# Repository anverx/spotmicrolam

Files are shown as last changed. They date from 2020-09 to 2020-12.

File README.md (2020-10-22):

# spotmicrolam
SportMicroAI the lean and mean edition.
The design is inspired by MicroSpotAI but developed from scratch.
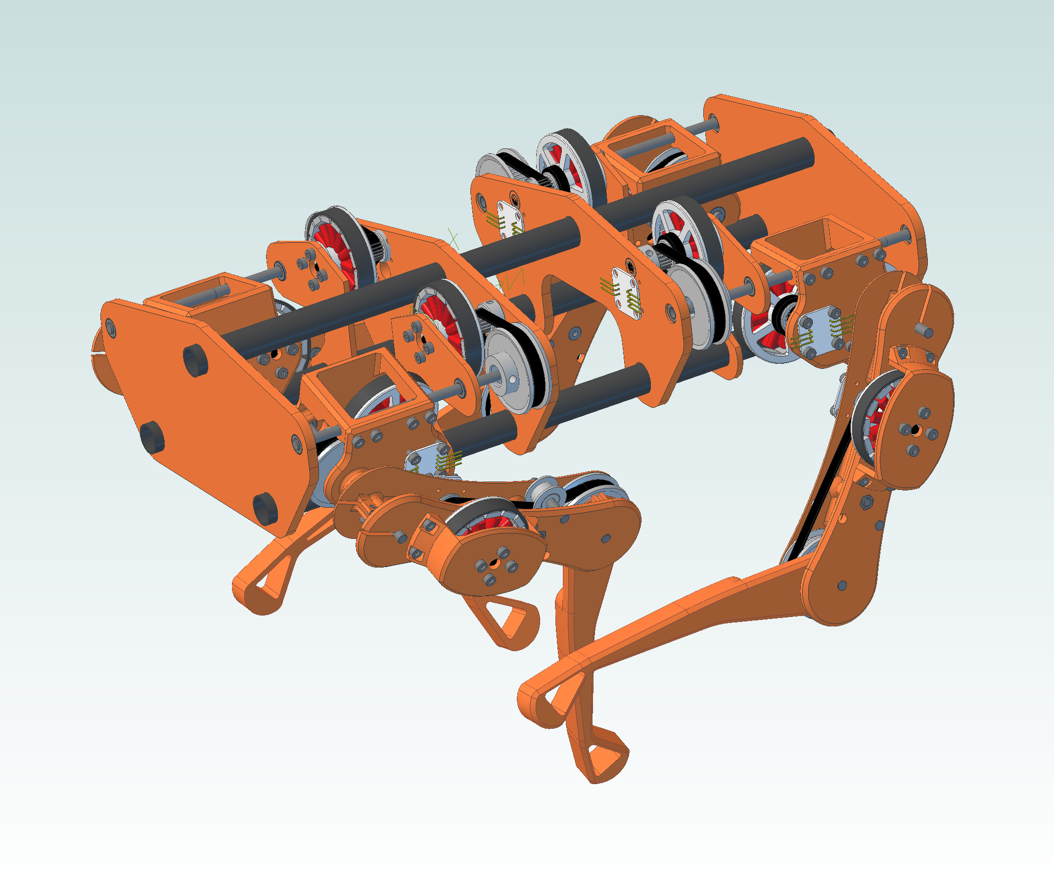
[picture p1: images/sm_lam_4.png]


## Design goals of the project:
* Cheap, under 500e, ideally towards 300e
* Off the shelf components and 3D printed parts only
* Designed parts optimized for easy printing, minimal or no supports
* Optimize for weight as the motors are underpowered
* bldc motors

## Challenges:
At the moment the biggest challenge are the motor drivers.  There are plenty of cheap brushless motors for aircrafts, and they should work fine.  
The ESC however are geared towards flying, they offer no reverse rotation or holding torque.  Finding the right ESCs and controlling them is an interesing excersize. 

## Key Ingredients
* 5010 BLDC motors, ~14e per piece
* Some bldc driver ~10e per piece if i can make HMBGC work, may need something else for more current
* Rotary encoder, at the moment AS5600 (single i2c adderess? meh), readymade module (~2e a piece)
* Bearings, pulleys, belts, shafts etc. under 30e per leg
* Carbon fiber pipes for body structure ~40e
* Raspberry Pi or Orange Pi + arduino clone for the brain ~40e

So, 26e (per motor) x 12 = 312
30e (per leg) x 4 = 120

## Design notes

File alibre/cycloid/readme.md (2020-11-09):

# Poorman's guide to calculating the cycloid disk shapes

[//]: # (This is a comment)

* There are some good references
  * [video on cycloids](https://www.youtube.com/watch?v=SWIx3GgqrAg)
  * [cycloid disk design in fusion](https://www.youtube.com/watch?v=jQ6LQBFZXmU)

* Compute the formulas using [the calculator](http://www.otvinta.com/cycloid.html), you will need the following parameters:
  * outer diameter
  * pin diameter
  * pin number
  * excentricity
* Graph the firmulas and save as svg using an online [graphing calulator](http://fooplot.com/)
  * use the parametric plot option
  * paste the formulas for x and y from the previous steps (change `u` to `s` where appropriate)
  * set s from 0 to 1 (plus 1 step),  set the step to 0.001 (or less)
  * in the display section untick grid, axes, tick marks and numbers

* If your CAD is unhappy with svgs [convert to dxf](https://cloudconvert.com/svg-to-dxf)
> after all Alibre is unable to assimilate splines generated with external applications, bummer

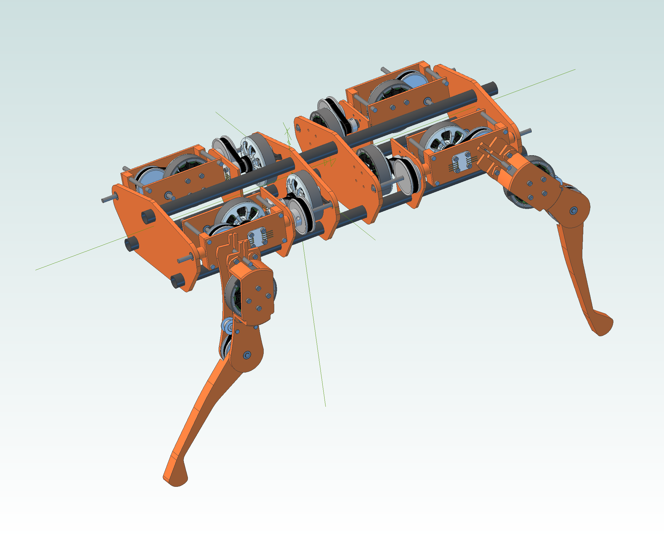
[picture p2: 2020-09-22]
images/sma_lam.png

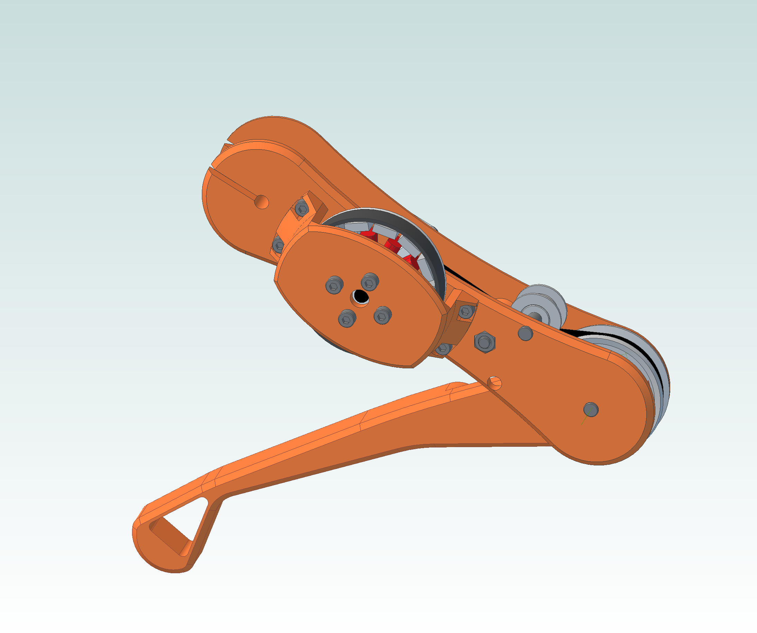
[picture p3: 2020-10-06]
images/Leg.png

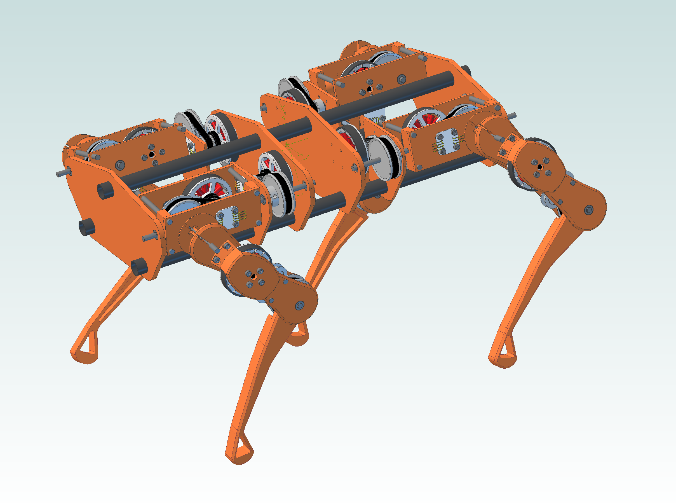
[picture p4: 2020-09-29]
images/sma_lam_2.png

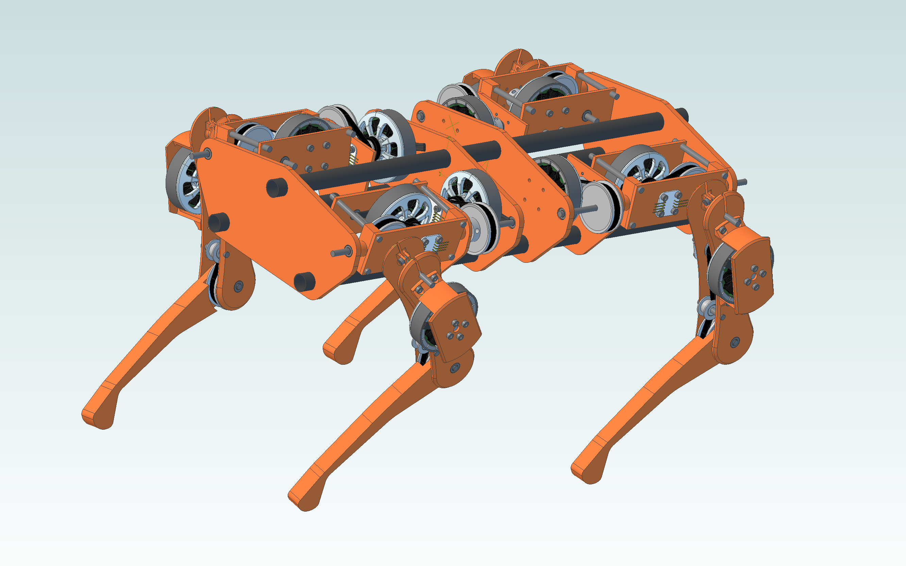
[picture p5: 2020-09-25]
images/sma_lam_1.png

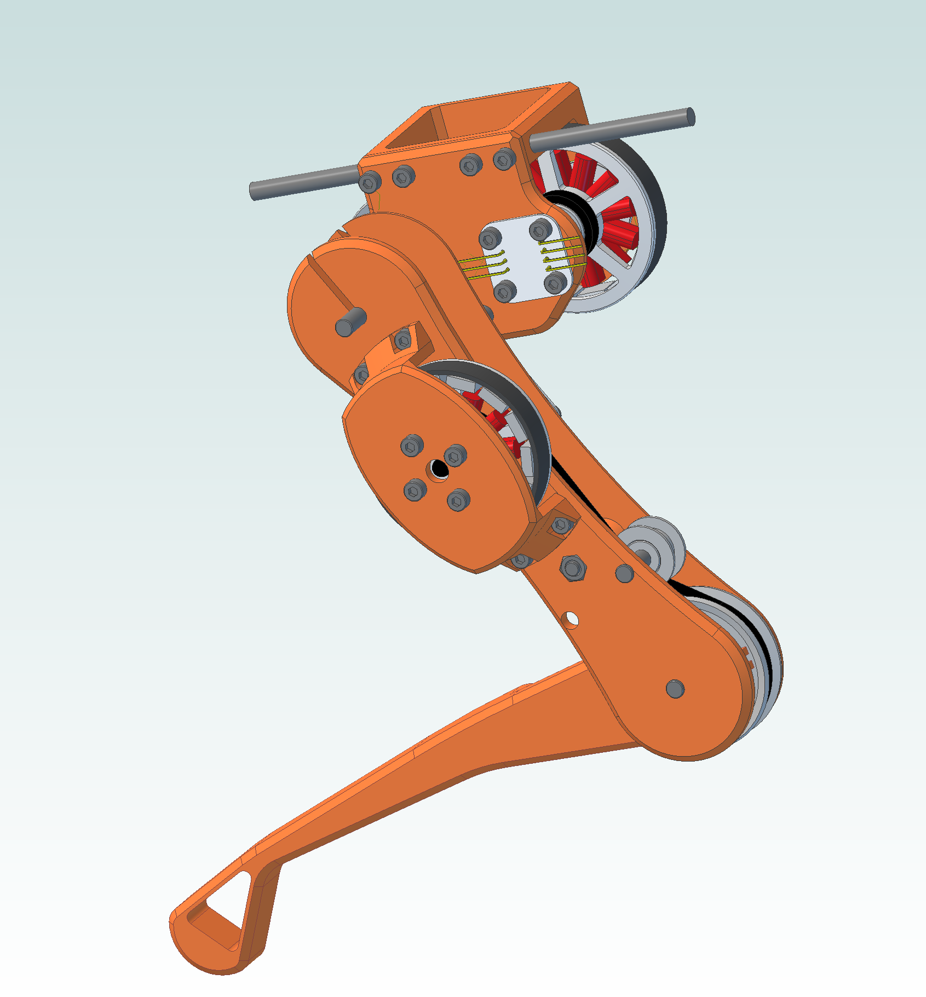
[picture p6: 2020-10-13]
images/shoulder_1.png

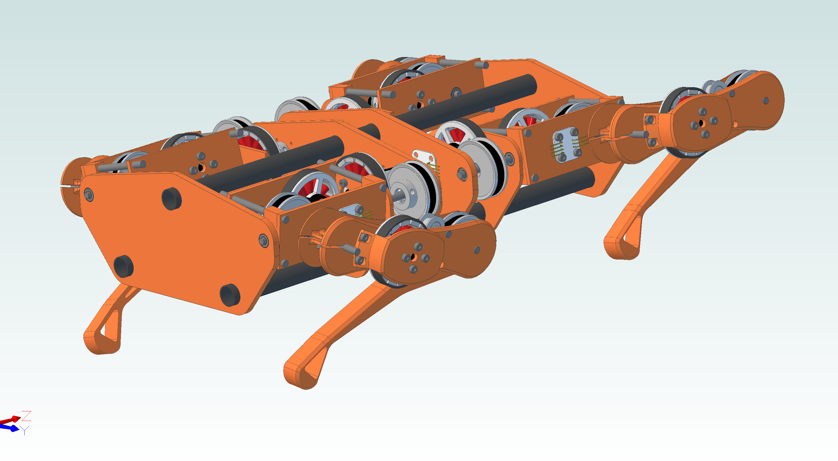
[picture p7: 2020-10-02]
images/sma_lam_3.png

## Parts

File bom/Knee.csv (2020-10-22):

Quantity | Part Number | Part Name | Revision | Comment | Estimated Cost
1 |  | Knee motor brace |  | Printed
2 |  | Shaft 5x30 |  | aliexpress: .5e x 3 | 1.5
1 |  | Idler GT2 smooth |  | aliexpress: 1e x 2 | 2
1 |  | Bearing 5x10x4 |  | aliexpress: .3e x 3 | 1
1 |  | Elbow outer |  | Printed
14 |  | Bolt M3x6 socket
1 |  | AS5600 magnetic sensor module |  | aliexpress: 2.6 x 1 | 2.6
1 |  | Elbow |  | Printed
1 |  | Knee belt |  | aliexpress: 1.2e x1 | 1.2
1 |  | Pulley GT2 20T |  | aliexpress: .4e x1 | 0.4
1 |  | Motor shaft |  | Comes with motor
1 |  | Pulley GT2 60T |  | aliexpress: 3.4e x1 | 3.4
1 |  | 5010 motor |  | aliexpress: 13e x1 | 13
1 |  | Bolt M4 socket
1 |  | Nut M4

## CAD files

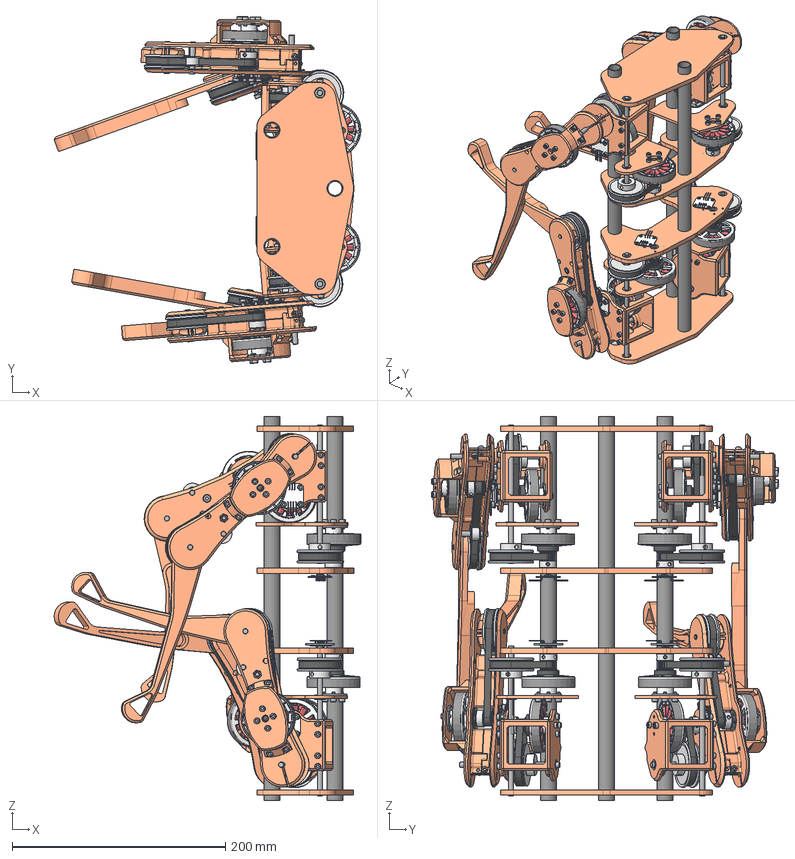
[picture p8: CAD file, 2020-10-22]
step/full.stp
287.6 x 325.4 x 360.0 mm

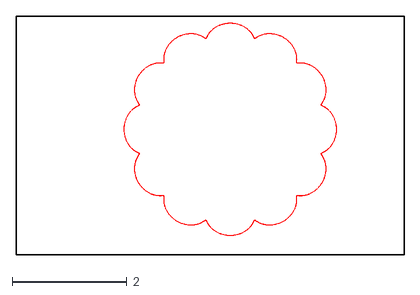
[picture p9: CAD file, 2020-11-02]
alibre/cycloid/cycloid.dxf
6.77 x 4.17

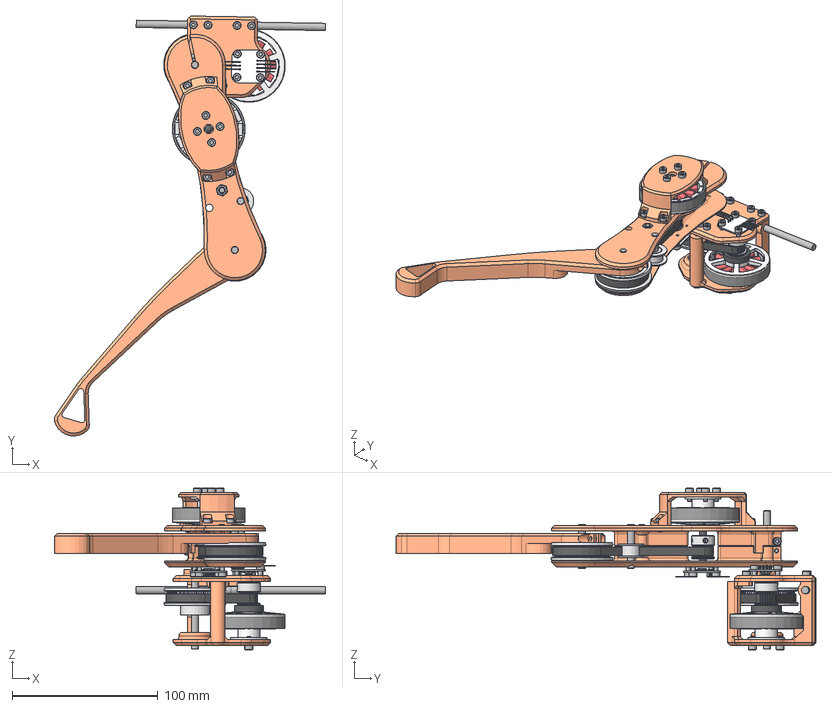
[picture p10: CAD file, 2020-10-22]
step/Shoulder knee.stp
186.3 x 288.3 x 111.0 mm

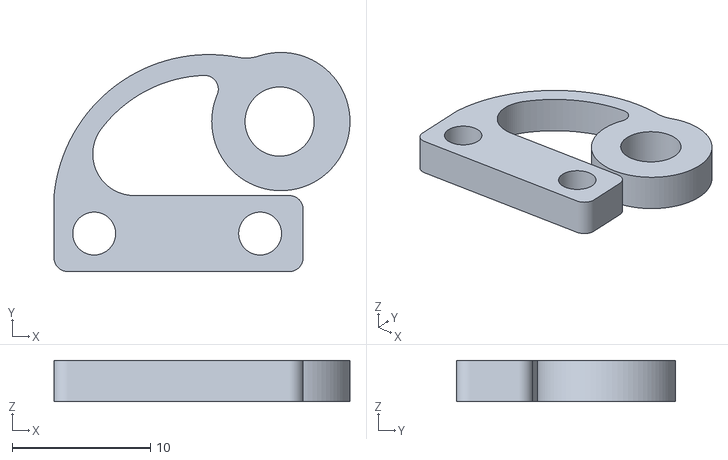
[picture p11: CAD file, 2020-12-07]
stl/Belt tensioner.stl
21.4 x 15.8 x 3.00

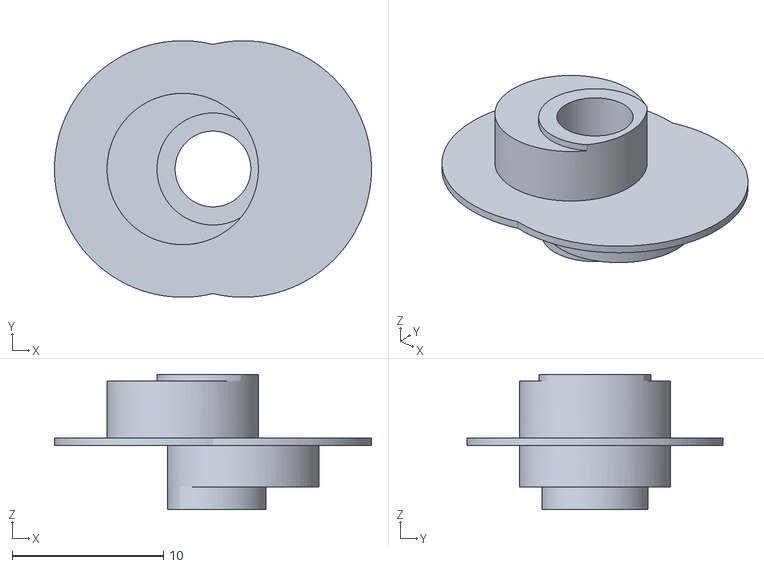
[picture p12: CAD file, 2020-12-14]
stl/cycloid/eccentric cam for bearings.stl
21.0 x 16.9 x 8.95

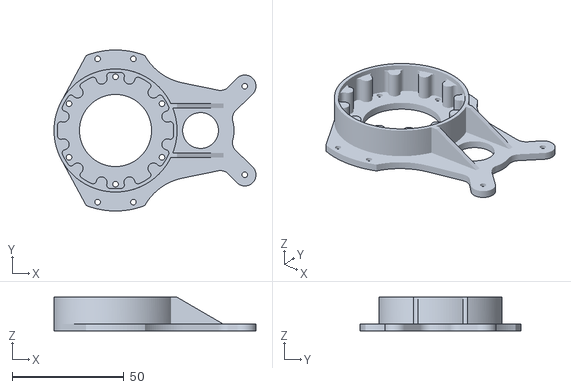
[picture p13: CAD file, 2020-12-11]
stl/cycloid/Stator13 with shoulder plate.stl
90.3 x 72.0 x 15.0

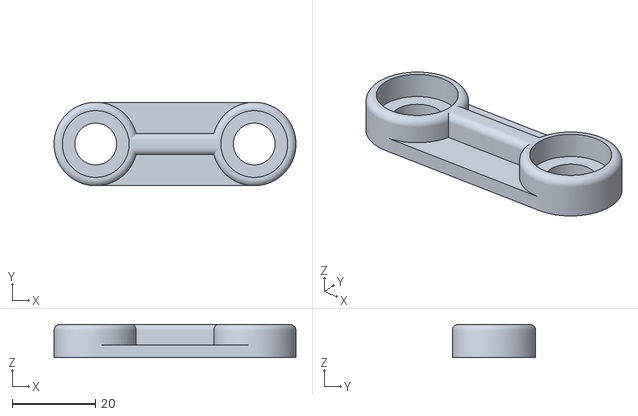
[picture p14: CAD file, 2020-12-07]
stl/knee belt jig 158 - 38mm.stl
58.0 x 20.0 x 8.00

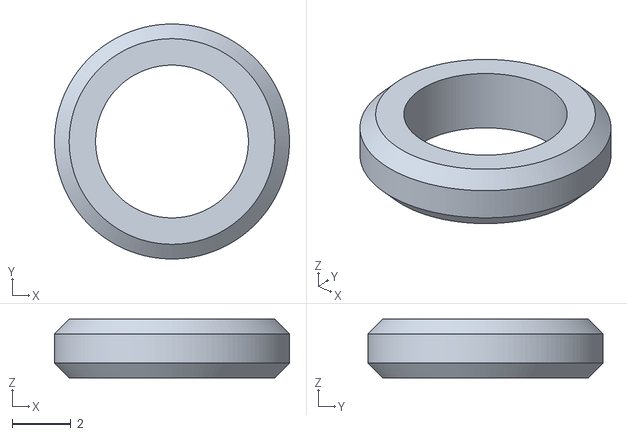
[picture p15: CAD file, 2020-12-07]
stl/5mm shaft spacer.stl
8.00 x 8.00 x 2.00

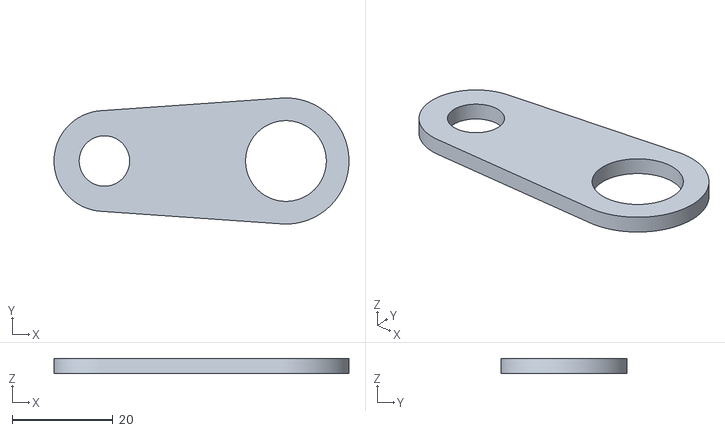
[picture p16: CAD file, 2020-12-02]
stl/cycloid/Bearing alignment helper.stl
58.5 x 25.0 x 3.00

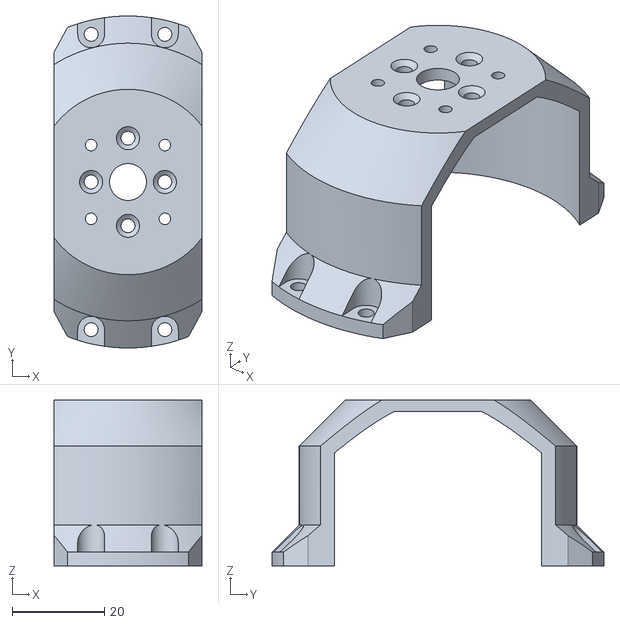
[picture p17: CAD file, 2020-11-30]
stl/cycloid/motor brace cycloid.stl
32.0 x 72.0 x 36.0

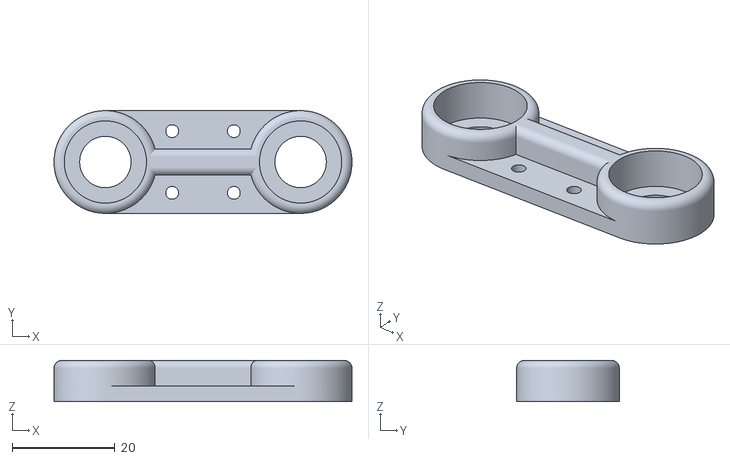
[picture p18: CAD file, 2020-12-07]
stl/knee belt jig 158.stl
58.0 x 20.0 x 8.00

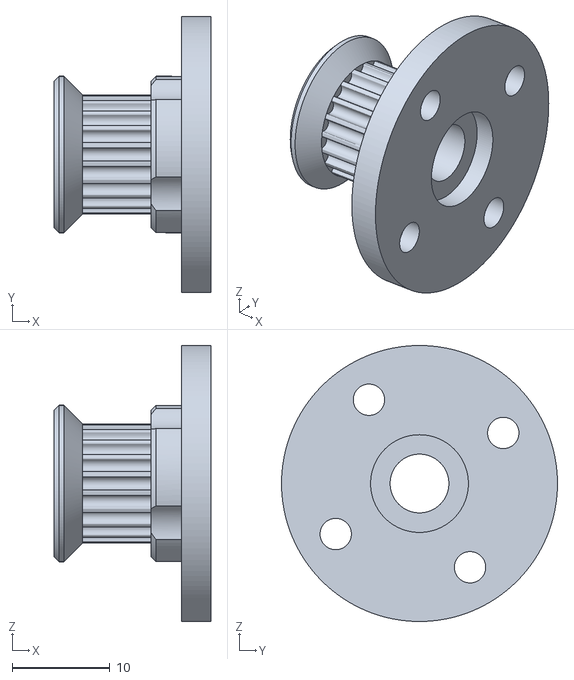
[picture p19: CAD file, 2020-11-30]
stl/cycloid/Pulley GT2 20T 4 print.stl
16.0 x 28.2 x 28.2

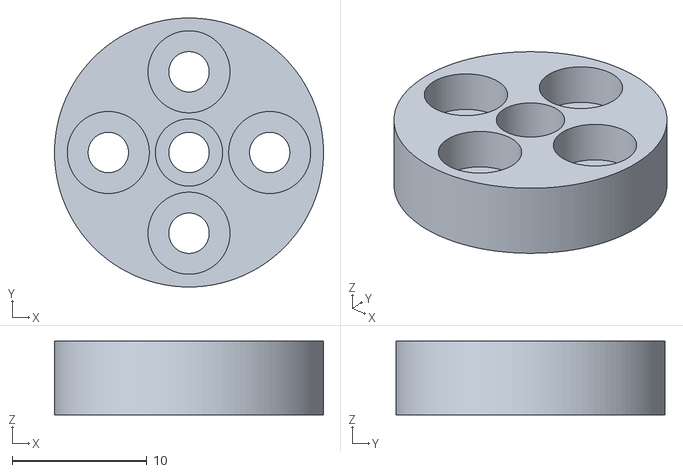
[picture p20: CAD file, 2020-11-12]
stl/motor adapter 5mm.stl
20.0 x 20.0 x 5.50

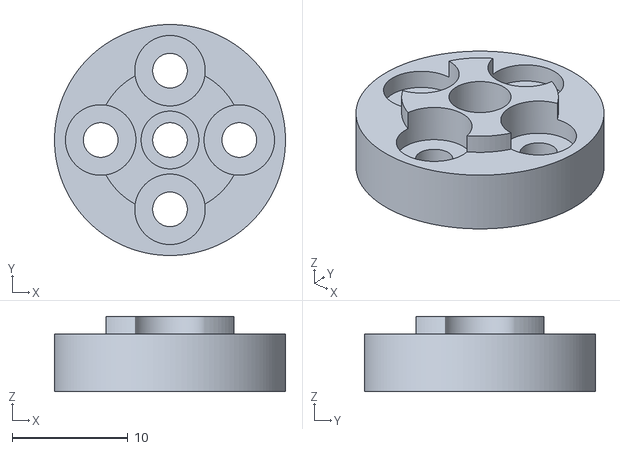
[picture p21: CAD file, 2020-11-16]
stl/cycloid/motor adapter 5mm.stl
20.0 x 20.0 x 6.50

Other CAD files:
stl/eccentric cam bore 5.stl
stl/cycloid/cycloid disk v3.stl
stl/eccentric cam flange bore 5.stl
stl/cycloid/ouput stage.stl
stl/Angle indicator.stl
stl/Elbow outer.stl
stl/Elbow.stl
stl/Knee motor brace.stl
stl/Pulley GT2 20T 4 print.stl
stl/Pulley GT2 20T bore 5 4 print.stl
stl/Pulley GT2 20T bore 6 4 print.stl
stl/Pulley GT2 60T 4 print bore 5.stl
stl/Pulley GT2 60T 4 print.stl
stl/Shaft adapter.stl
stl/Shoulder knee.stp
stl/Shoulder v2 bearing 16.stl
stl/Shoulder v2.stl
stl/Stator spacer.stl
stl/Stator13.stl
stl/Wrist thin.stl
stl/cycloid disk v3.stl
stl/cycloid/Stator13.stl
stl/cycloid/eccentric cam.stl
stl/eccentric cam.stl
stl/full.stp
stl/knee belt jig 280.stl
stl/ouput stage.stl
stl/shoulder inner v2 bearing 16.stl
stl/shoulder inner v2.stl

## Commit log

2020-09-24 Added bom for the knee
    [Knee.csv]
2020-09-25 more work on the knee
    [Knee motor brace.stl]
2020-09-25 Added bridges for printing
    [Knee motor brace.stl]
2020-09-25 Finished legs, knees are symmetrical but wrists are not.
    [Knee.csv]
2020-09-27 Replaced motor model, the one snagged from cgtrader had completely wrong dimensions.
    [Elbow outer.stl, Elbow.stl, Knee motor brace.stl]
2020-09-28 Relaced all the motors, made body more compact, also sortened. Redesigned 20T pulley for printing.
    [Pulley GT2 20T 4 print.stl]
2020-09-28 Added stiffners in the knee, should be more rigid now
    [Elbow outer.stl, Elbow.stl, Knee.csv]
2020-09-29 Resized motor, more work on the knees
    [full.stp]
2020-10-01 Added a bolt that holds the knee together.
    [full.stp]
2020-10-01 More work on the knee, compacting the body further.
    [Elbow outer.stl, Elbow.stl, Knee motor brace.stl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]
2020-10-02 Moved the bearings inside the wrist
    [Elbow outer.stl, Elbow.stl]
2020-10-05 Added gt2 60T pulley
    [Pulley GT2 60T 4 print.stl, Shaft adapter.stl]
2020-10-08 Much work on the shoulder
    [knee belt jig 158.stl, knee belt jig 280.stl]
2020-10-08 Removed unused motor model
2020-10-09 added 60T pulley with bore 5
    [Pulley GT2 60T 4 print bore 5.stl]
2020-10-12 Shoulder is ready for first print
    [Shoulder v2 bearing 16.stl, Shoulder v2.stl, shoulder inner v2 bearing 16.stl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]
2020-10-14 Correctingh pulley sizes
    [Pulley GT2 20T bore 5 4 print.stl, Pulley GT2 20T bore 6 4 print.stl, knee belt jig 280.stl]
2020-10-15 adjusting belt rig for bearings
    [knee belt jig 158.stl]
2020-10-16 Reinforcement for shoulder cage
    [shoulder inner v2.stl]
2020-10-21 Quick update of the step files
    [Shoulder knee.stp, full.stp]
2020-10-22 Compacting the torso some more. Fresh pic
    [Knee.csv, Shoulder knee.stp, full.stp]
2020-11-02 Some preliminary work on cycloid reducer
    [cycloid.dxf]
2020-11-09 Initial comit for cycloid redicer
    [Stator spacer.stl, Stator13.stl, cycloid disk v3.stl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]
2020-11-10 Ouptut stage for the cycloid
    [Angle indicator.stl, ouput stage.stl]
2020-11-12 Some work on cycloid
    [eccentric cam bore 5.stl, eccentric cam flange bore 5.stl, motor adapter 5mm.stl]
2020-11-14 Packaging cycloid with the motor
2020-11-16 Modular design of the cycloid
    [Stator13.stl, cycloid disk v3.stl, eccentric cam.stl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]
2020-11-30 Integrating cycloid into shoulder
    [Pulley GT2 20T 4 print.stl, Stator13 with shoulder plate.stl]
2020-11-30 just double checking the stl
    [motor brace cycloid.stl]
2020-12-02 small changes in shoulder
    [Bearing alignment helper.stl]
2020-12-07 some belt hacks
    [5mm shaft spacer.stl, Belt tensioner.stl, knee belt jig 158 - 38mm.stl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]
2020-12-11 Fixes to cycloid stator
    [Stator13 with shoulder plate.stl]
2020-12-11 New type of bearing added
2020-12-14 Bearings added to cycloid disks
    [eccentric cam for bearings.stl]
